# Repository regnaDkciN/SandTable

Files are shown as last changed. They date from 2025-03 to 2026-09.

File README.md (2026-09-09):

# **NOTE:** 
This GIT archive contains several versions of the sand table described within this document.  Each version contains different hardware and firmware capabilities.  The versions are:
* **MySandTable** - This was the original version and is described fully in this readme file.  It used the original Arduino board.
* **MySandTable2350** - This version upgraded to use the Adafruit Metro 2350 board.  This version contains many upgrades from the original.
* **MySandTableFreeRTOS** - This version uses the Adafruit Metro 2350 and adds FreeRTOS support.
* **MySandTableFreeRTOSExp** - This was originally an experimental version, hence the name, but has become the  main development version.  It has many upgrades and fixes many bugs.
* **MySandTableSdFat** -This version adds access to the Metro 2350 board's SD card.  It allows for placing new shape files in the SD and randomly selects files to shape execute.

# Sand Table
Sand Table
I have always been interested in sand tables, but most required more carpentry work than I could handle, and were too expensive for my budget.  Then I came across  the Instructable of [<u>World's First Cycloid Art Table: How I Built This Arduino-Powered Spirograph Machine</u> by NewsonsElectronics](https://www.instructables.com/Worlds-First-Cycloid-Art-Table-How-I-Built-This-Ar/).  This was finally a reasonable design that I could handle.

My background is in real time embedded firmware, so the software wasn't a problem.  Woodworking is pretty much out of my league.  However, this project was mainly laser cut, and my local library had a laser cutter available, so I learned how to use it with pretty good results.  Along the way I made quite a few changes to the design, and am pretty happy with the outcome.

This site describes some of the modifications I made on the way. Notable changes include:
* Addition of a home limit sensor with corresponding firmware.
* Addition of a 3D printed Arduino bumper for mounting the Arduino UNO board to the base.
* Addition of a top ring to hold a plexiglass window.
* Greatly modified Arduino sketch which adds many new shapes, randomization functions, and fixes several problems that were encountered with the original sketch.
* Addition of a power switch with associated 3D printable box.
* Replacement of the small wooden gears with new 3D printed ones.
* The highly modified original software version for use with the Arduino UNO - *MySandTable*.
* A software version - *MySandTable2350* - that replaces the Arduino UNO with an Adafruit Metro RP2350 board.  As of 21-AUG-2025 this branch will no longer be updated.
* A software version - *MySandTableFreeRTOS* - that uses the FreeRTOS real-time operating system on the Metro RP2350 board.  As of 21-AUG-2025 this branch will no longer be updated.
* A software version - *MySandTableFreeRTOSExp* - that plans motion several moves ahead in order to help smooth out the motion.  This version was originally experimental, thus the 'Exp' suffix.  However, it is currently stable and is the preferred RP2350 version.  All future development and fixes will be done on this version.
---
# General Issues/Fixes/Useful Information

This was my first experience with laser cutters.  The Instructable included .DXF and .SKP files for the laser cut parts.  I couldn't make use of the .SKP file, but found that I could work with the .DXF files.  For these I used [QCAD](https://qcad.org/en/) which is a free, open source application for 2D CAD drafting.  The available laser cutter required .PDF files though.  I ended up using QCAD to edit the original .DXF file and produce a .SVG file.  Then I used [Inkskape](https://inkscape.org/?about-screen=1) to convert the .SVG file to .PDF.  The workflow was as follows:
1. Use QCAD to edit the original .DXF file.
2. Use QCAD to generate the .SVG file.
2. Use Inkscape to add text and other features to the .SVG file.
3. Use Inkscape to change cut lines to 0.1pt width (required by the laser cutter).
4. Use Inkscape to create the .PDF file which is used by the laser cutter.

## Wood Selection
Used Baltic Birch Plywood- B/BB Grade 1/8" / 3mm / 24"x24"  (https://makerstock.com/).  Liked the quality of the wood and the price was reasonable.

## Steel Ball
Instructable showed both 15mm ball and 8mm ball.  I experimented and ended up replacing the steel ball with stack of 4 each [3mm x 2mm magnets](https://www.amazon.com/dp/B09SLFSRBP).

## Sand
I originally used the recommended sand in the table but found it to cause jerky ball motion, and was pretty noisy. After an extensive web search, found  that [Shuffleboard Sand](https://www.amazon.com/dp/B08NFZFGQF) was an excellent replacement.  This produces much smoother and quieter movement.

## Magnets
The Instructable used a single 15mm x 3mm magnet on the end of the linear arm.  I stacked 2 each 15mm x 3mm magnets for better ball following: (https://www.amazon.com/dp/B0B5G6XS4J).  At one point I tried 3 stacked magnets, but found that 2 worked just as well.

## Miscellaneous Table Construction
* I found that the motors didn't originally line up vertically.  This may have been due to my motors not being sized exactly as the specified ones, or due to my lack of construction skills.  At any rate, I ended up with 3 spacers under the center (linear) motor, and none above it.  I also used 1 spacer below the outer (rotary) motor and 2 spacers above it.  Due to this, the small pillar needed to be modified slightly to fit correctly in my setup.  I cut 3mm from lip that goes over servo to account for extra spacer below.
Modified Small Pillar
* The Instructable wasn't very clear about the number of small rings needed to hold up the table.  I used 8 layers of small rings, which also accounts for the extra magnet that I used.  Similarly, it wasn't clear how many large rings should be used on the table.  I settled on 5 large rings because I wasn't sure about the ball size.  However, after deciding on using 4 each of 3mm x 2mm magnets in place of a steel ball, it is clear that I could have used 4 rings instead.
Rings Callout
* After assembly, I found that the table wasn't securely attached to the base, so it was too easy to attempt to pick the unit up and have the table detach from the base.  I did not want the table to permanently connect to the base since I knew that maintenance would then be impossible.  I decided on the simple approach of drilling  1/16" holes in the table vertical rods, and insert a wire through the hole to keep the table attached to the base.  This allowed for easy  detachment of the table from the base by simply removing the wires from the rods.
Retaining Wire
* The original holes for the potentiometers were too close to the Arduino UNO board.  I moved them to the center of the corresponding boards.  I also added labels as shown below.  After some use, I decided that the pot labels would be better placed above the potentioneters, but left them as is.
 Front Low Level View
* I found that the potentiometer face plates were not very secure.  To fix this, I carefully drilled 5/64" holes through the faceplates and base plate and inserted small nails.
* I originally added rubber feet to the bottom of the base.  It turned out that they prevented easy shaking of the table to clear it, which is very useful when debugging.  I replaced the rubber feet with felt pads and found that these were much better.  The feet I ended up using were [these](https://www.amazon.com/Black-Self-Adhesive-Felt-Bumpers/dp/B07DYQJRDB/ref=sr_1_1?sr=8-1).
* I have added a 3D printed part - "Bezel3.stl" - to strengthen the face plate panels (the ones that hold the pots and the UNO face plate).  It contains a channel that the top of the face plate panels seat into and provides some rigidity.  It also helps to protect the wiring of the electronic parts.
Bezel

----

# GEARED PARTS
I had several problems with the gears.  This section contains information regarding my findings and fixes.

## Dowel Rods
I couldn't find the tapered dowel rods that were recommended in the Instructable write-up.  I ended up using [1/8" wooden dowel rods](https://www.amazon.com/dp/B0CXDDGRFK) for the geared parts .  This required changing all the dowel rod holes in the geared parts to 3 mm.  The "Modified Parts" files contain the modified parts.  Note that two of the large gear are required.

## Bearing
I couldn't find recommended bearing.  Instead I used a [F695-2RS Bearings, 5x13x4mm Ball Bearing](https://www.amazon.com/dp/B0CZ6RBJSZ) which worked out well.

## Reversed Linear Gear
I accidentally mounted the linear gear in the opposite direction from how the Instructable  video shows it.  This required several modifications to the Arduino sketch.  If you use my program, you may want to flip the linear gear as I did to avoid problems with my code.
Flipped Linear Gear

## Large Rotary Gear
* The Instructable was ambiguous regarding the large rotary gear.  I found that it should be doubled up (i.e. one on top of the other) and in my case I needed the center hole diameter to be 12.7mm.  The included  "Modified Parts" files have have been updated with these changes.  Note that two of the large gear are required.
* Neither of the laser cut small gears worked well.  Both were a little too wide, probably due to a difference in kerf width between the laser cutter I used and the one used in the Instructable.  I experimented and came up with 3D printed gears to replace both of them.
* Doubled Up Large Gear

## Small Gears
* The small outside (rotary axis) gear needed to be at least 5mm thick, which is OK since the large rotary gear is doubled up.  The included **Small Gear Thicker.stl** file can be used to 3D print  this thicker gear.  I used PLA for the gear with 30% infill and 0.2mm layer.  The PLA gear has worked great with over 100 hours of run time, but I would guess that ABS or PETG would be better.
* The small center (linear) gear did not catch the motor shaft enough and gave constant problems.  I created a new 3D printed gear which adds a 2.4mm long 11mm diameter shaft which fits in the center hole of the large gear, and gives more area of contact between the small gear and the motor shaft.  The included **Small Gear With Bushing.stl** file contains the result. I used PLA for the gear with 30% infill and 0.2mm layer.  The PLA gear has worked great with over 100 hours of run time, but I would guess that ABS or PETG would be better.

# Motors
* As previously mentioned, I had problems with motor height alignment.  I ended up with 3 spacers under the
  center motor, and none above.  Used 1 spacer below the outer motor, and 2 above.
  Rotary Motor Spacers
  Linear Motor Spacers
 
* I used these [Nema 17 stepper motors (17HS4023)](https://www.amazon.com/dp/B0C36D34F5).  Their original cables were too long which made it hard to stow them on the base.  I replaced the original motor cables with shorter [(500mm) stepper cables](https://www.amazon.com/dp/B07Q12B6K5?ref_=ppx_hzod_title_dt_b_fed_asin_title_0_0).  These solved the size problem, but weren't wired the same as the original cables.  In order to make them work, the 2 middle conductors needed to be swapped.  I just used brute force and pulled them out of on end, swapped them, then pushed them back in.  This worked OK and I have had no problems with them.

* The screws from the original motors were too short.  I replaced the center motor screws with m3 x 6mm, and the outer motor screws with m3 x 14mm.

* The holes in the motor spacers were too small.  I enlarged them using a 7/64" bit, which worked out well.

# CNC Shield
* I used the recommended [Arduino CNC Shield](https://www.amazon.com/dp/B08KFYKKN4).  In bringing it up I had several major issues.  Some were my fault, and some were due to the broken motor drivers that were included with the shield.  In the end, these were the problems and workarounds:
	+ Not one of the 4 included stepper drivers functioned at all.  In fact, one of the drivers caused the CNC shield's fuse to blow, and blew a trace to the X-Axis.  The Instructable recommended the use of other drivers, and I bought them, but I wanted to get it to work with the original drivers before I switched to the good ones.  I should have just started with the [TMC2209 Stepper Drivers]( https://www.amazon.com/dp/B08SMDY3SQ), and would recommend everyone do the same.  I ended up bypassing the fuse, and using the shield's Y- and Z-Axis instead of the X- and Y-Axis.  The Y-Axis now controls the linear in/out axis, and the Z-Axis now controls the rotary axis.
	+ The Instructables author also contributed two enhancements for the CNC shield which I applied to my setup. Neither of these enhancements is absolutely necessary, but I think they are useful.  Both of the modifications can be found at the Instructables site as [Arduino CNC Shield V3 - Enhanced Capabilities and Features](https://www.instructables.com/Arduino-CNC-Shield-V3-Enhanced-Capabilities-and-Fe/).  I modified the shield to supply power to the Arduino, and to add the ability to enable the axes individually (based on Y- and Z-Axes).

# Stepper Drivers
* The DRV8825 stepper drivers that came with the CNC shield were total junk.  Not a single one of them worked.  Trying to use one of them resulted in blowing the CNC shield fuse, and damaging the X-Axis socket.
* As recommended, I used [TMC2209 Stepper Drivers]( https://www.amazon.com/dp/B08SMDY3SQ) instead of the ones that came with the CNC shield.
* Setting the motor current of the TMC2209 stepper driver is well explained [HERE](https://www.youtube.com/watch?v=VcyGzXIZm58).  The desired current for these motors is less than 700mA per phase.

  		Vref = Desired Current x 0.71 x 2 
  		     = 0.99V for 700mA per phase
  		
# Arduino UNO
* I used the Arduino UNO that came with the CNC shield.
* Found that mounting the Arduino is difficult, especially when gear assembly is already in place.  Created a 3D printed Arduino bumper with side mounting holes to help in placing the Arduino.  See the included **Arduino Bumper.stl** file.
* Found that M3 screws fit nicely into 7/64" holes in plywood.  Used M3 screws to mount the Arduino with bumper to base plywood.
Arduino Mount

# Power Box
* I used this [Power supply: 12V 8A](https://www.amazon.com/dp/B0CL1RX1TX).  It is definitely overkill, but works well and was not too expensive.
* I wanted a clean way to connect power to the sand table, so I decided to use a 3D printed power box with a power connector that matched the power supply, and a switch.  The switch box with lid is included as **Power Box.stl** and **Power Box Lid.stl**.  Used PLA, 20% infill, and 0.2mm layer height for the print.
Power Box 1
Power Box 2
* I used this [Power supply connector](https://www.amazon.com/dp/B0D9JGXBJB).
* I used a switch that I had on hand, similar to [this one](https://www.amazon.com/uxcell-Position-Button-Rocker-Switch/dp/B0727PBJLV).
* Drilled two 3/16" holes through the base of the power box and the base of the sand table for mounting.  Used m3 x 5mm screws to secure the power box to the base.

# Rotary Home Sensor
* I wanted to be able to home the axes to a known starting position so that things like text could be displayed in a consistent manner.  So I added a home limit reed switch using GPIO 5.  This GPIO pin was originally the X axis direction pin, but since I am using Y and Z, the X axis direction pin was available.  Here's an example of some text that will always print upright due to the axes being homed.
JMC
* I used [Reed Switch Reed Contact Normally Open (N/O) Magnetic Induction Switch (2mm*14mm)](https://www.amazon.com/dp/B07RS2M9TR) to sense the pointer magnet.  There was no need to add any additional magnets.
* I created and 3D printed a mount for the reed switch, which is included as **Reed Switch Mount.stl** and mounted it near the Brightness pot. Used PLA, 15% infill, and 0.2mm layer height for the print.  Used m3 x 4mm screws to secure the mount to the horizontal member.   Drilled a 3/16" hole in the horizontal member near the mount to pass the sensor wires through to the Arduino.  Used 
Home Sensor Mount
* Updated the Arduino sketch Home() function to use new home limit switch.  See the .ino file.
* The Home() operation behaves as follows:
    ```
 	   Extend the in/out axis all the way out
	   If already on the home sensor
	       Then rotate CCW till off of the sensor
	   Rotate CW till the home sensor is detected
	   Rotate CCW by the amount specified by HOME_ROT_OFFSET
	   Retract the in/out axis all the way in
	   Initialize all position and motor variables to position (0,0)
	   Enable both motors
* Note that an offset may be applied (HOME_ROT_OFFSET) in order to align the rotation of the origin as desired.

# Miscellaneous Electronics
## Potentiometers
* I used these [10K pots](https://www.amazon.com/dp/B0BRGX2FTL).

## LEDs
* I use these [LEDs](https://www.amazon.com/gp/product/B0C8HTH282)
* Drilled a 5/32" horizontal hole into the upper ring to route LED cable into the ring vertical hole.
* Drilled a 5/16" hole in vertical support to pass LED cable through.
* Added a  [2 Conductor JST Connector](https://www.davesrce.com/product-page/jst-connectors?gQT=1) to attach the LEDs to the Arduino UNO so that top may easily be disconnected from base.
* Added a [Self-Adhesive Super Klip](https://www.amazon.com/Super-Glue-KW10-12-Klips-120-Pack/dp/B00FY8WHEU) as a cable organizer for the LED cable.
![LED Connector 1](https://i.imgur.com/DXwuwZe.jpeg)
![LED Connector 2](https://i.imgur.com/6Vc9H8k.jpeg)

## MOSFET 
* Used [Power MOSFET IRFZ44N](https://www.amazon.com/dp/B0CHQ8QJ5K).  Note that the parts list on the Instructable is incorrect and specifies BD139N transistor when IRFZ40N should be used.  IRFZ44N is an acceptable replacement.
* Added a 100K resistor between the MOSFET gate and ground (source) to keep the LEDs from turning on full brightness at power-up.
* Used metal 3mm x 8mm bolt to secure MOSFET to left Arduino mounting wing through hole drilled in base.  Also use 2  m3 washers for spacing and heat dissipation.
![MOSFET Mount](https://i.imgur.com/AMYUQlH.jpeg)

# Window
* Created a top outer ring that is used to hold the acrylic window.  The attached **Window Holder no Text.pdf** file corresponds to this window holder.
* Used [12" x 12" Clear Cast Acrylic Sheet]( https://www.amazon.com/dp/B0BBQ8B41F) for the window.  Cut it circular with laser the cutter using the attached **Window.pdf** file.  It fits inside top Window Holder ring.
* Found that the acrylic widnow generates enough static to attract the Shuffle Board Sand.  I don't know if real sand would have the same problem, but the shuffle board sand really did.  I was a little skeptical, but decided to try an [Anti-static CRT Cleaner](https://www.amazon.com/dp/B00UM9C04S?ref_=pe_123509780_1038749300_fed_asin_title) and found that it worked well and completely eliminated the problem with sand clinging to the acrylic window.  I would recommend its use.
* Generated simple 3D printed cylinders (**Window Knob.stl**) to use as knobs for the window.  Used PLA, 20%infill, and 0.2mm layer height for the print.  Attached them to the window with glue.
![Window Knob](https://i.imgur.com/bxLPUnK.jpeg)

# Software

The included Arduino sketch (**MySandTable.ino**) was based on the [Instructable]( https://www.instructables.com/Worlds-First-Cycloid-Art-Table-How-I-Built-This-Ar/) Arduino sketch **working10iteration.ino**.  It was, however, almost completely rewritten to add features and make it more understandable.  A few of the changes were:
* Re-formatted, including renaming variables and functions, using consistent indenting, and generally cleaning up the code.
* Uses Y- and Z-Zxes of the CNC shield instead of X- and Y- of the original.  This was due to the X-axis hardware on my CNC shield being damaged.
* Used some slightly different algorithms in a several spots.
* Added several more shapes, and randomization functions for each shape.
* Many more changes to fix anomalous behavior and enhance operation.

## Serial Logging
The **SerialLog.h** file was added to help with making groups of data logging to be easily enabled or disabled.  It contains macros to selectively print information based on some user-defined level macros.
Prints will only generate output if the corresponding macro is set to `true`.  `SerialLog.h` should be placed in the same directory as the Arduino sketch (`MySandTable.ino`).

Logging macros include:
* `LOGF(pBuf, bufSize, level, ...)` <br>
	This macro implements a formatted print.  It uses a printf style format to create a string to print.  The limitation of this macro is that it cannot print 32-bit integers or floats.  Its arguments are:<br>
&nbsp;&nbsp;&nbsp;&nbsp;`pBuf` : A pointer to a buffer to hold the formatted output data.<br>
&nbsp;&nbsp;&nbsp;&nbsp;`bufSize`: The size, in bytes, of `pBuf`.<br>
&nbsp;&nbsp;&nbsp;&nbsp;`level` : A value that will be evaluated as either `true` or `false`. If `true`, then the printf style string will be sent out the serial port.  
&nbsp;&nbsp;&nbsp;&nbsp;&nbsp;&nbsp;&nbsp;&nbsp;&nbsp;&nbsp;&nbsp;&nbsp;&nbsp;&nbsp;&nbsp;&nbsp;Otherwise no action will be taken.<br>
&nbsp;&nbsp;&nbsp;&nbsp;`args`: This is a printf style string with optional additional arguments.
* `LOGU(level, v)`<br>
	This macro implements an unformatted print.  It simply prints the given single value as long as `level` evaluates to `true`.  Its arguments are:<br>
 &nbsp;&nbsp;&nbsp;&nbsp;`level` : A value that will be evaluated as either `true` or `false`.  If `true`, then the value will be sent out the serial port.
&nbsp;&nbsp;&nbsp;&nbsp;&nbsp;&nbsp;&nbsp;&nbsp;&nbsp;&nbsp;&nbsp;&nbsp;&nbsp;&nbsp;&nbsp;&nbsp;Otherwise no action will be taken.<br>
&nbsp;&nbsp;&nbsp;&nbsp;`v`: This is the value that will printed if `level` evaluates to `true`.  It can be any valid printable data type.

The top of MySandTable.ino contains macros to enable/disable specific types of information to be sent via the serial port as well as macros to simplify logging macros use.
```
/////////////////////////////////////////////////////////////////////////////////
// S E R I A L   L O G   S E T T I N G S
//
// The following #defines are used in conjunction with SerialLog.h to selectively
// enable/disable printing of certain information.  Setting any macro to 'true'
// enables the specific level of data to be printed.  Setting any macro to 'false'
// disables printing of the specific data level.
/////////////////////////////////////////////////////////////////////////////////
#define LOG_DEBUG        false      // Log debug related info. Not normally  needed.
#define LOG_VERBOSE      false      // Log verbose info. Not normally needed.
#define LOG_INFO         true       // Log some useful extra info.
#define LOG_STEP         false      // Log data to help stepping ShapeArrays
#define LOG_CYCLES       true       // Log useful info regarding remaining cycles.
#define LOG_ALWAYS       true       // Log data unconditionally.
#define LOG_BUF_SIZE     60         // Important: size of formatted log buffer.
                                    // All formatted log strings are limited to
                                    // this size.
char LogBuf[LOG_BUF_SIZE];          // Buffer for formatting log data.

// Logging macros to ease log use.
#define LOG_F(level, ...)   LOGF(LogBuf, LOG_BUF_SIZE, level, __VA_ARGS__)
#define LOG_U(level, v)     LOGU(level, v)

```

* `LOG_DEBUG` - Setting this macro `true` will enable debug related information to be sent via the serial port.  This was mainly used to debug the SuperStar shape, and is normally set to `false` to disable sending its data.
* `LOG_VERBOSE` - Setting this macro `true` will enable verbose information to be sent via the serial port.  This was mainly used in early debugging of the movement generation code, and is normally set to `false` to disable sending its data.
* `LOG_INFO` - Setting this macro to `true` will enable informational data to be sent via the serial port.  The data sent by enabling this macro describes the call to the shape that is currently executing.  It includes the name of the function being executed, and a list of all of its arguments.  This macro is normally set to `true`. (A possible future project will use a Raspberry Pi Zero W to read this information, and save it along with a picture of the resulting table state.  Stay tuned.)
* `LOG_STEP`- Setting this macro `true` will enable the ability to single step the plotting of shape array data.  This can be useful for optimizing the memory footprint of any newly added shape array.  For example, by single stepping through a shape array, one may identify redundant or useless moves that may be removed.  This macro is normally set to `false`.
* `LOG_CYCLES`- Setting this macro `true` will generate cycle countdown information.  Certain shapes loop through multiple cycles before they complete.  Enabling this macro displays a countdown of the number of cycles remaining for the particular shape.  This macro is normally set to `false`, but if you like to have an idea of how much time is left when generating a shape, then set it to `true`.
* `LOG_ALWAYS` - This macro should always be set to `true`.  All data that should be sent unconditionally uses this macro.

A buffer that is used for formatting log data is also created here.  The buffer, `LogBuf[LOG_BUF_SIZE]`, must be sized large enough to handle the largest formatted log message.  `LOG_BUF_SIZE` is initially set to 60, which should be enough to handle all existing formatted log messages.

Two more macros (`LOG_F` and `LOG_U`) are also created here to make using the serial logger easier.  All logging done in MySandTable.ino uses one of these two macros.
 
 ## User Settable Constants
 The following macros are meant to be settable by the user depending needs.
 ```
 #define PAUSE_ON_DONE  false // Set to 'true' to pause when drawing finishes.
#define ROT_CAUSING_IN CCW   // Set to 'CW' if clockwise rotation causes IN movement.
                              // Set to 'CCW' if counter clockwise rotation causes IN movement.
```
 
* `PAUSE_ON_DONE` - This macro is used while debugging/testing.  If `true`, then execution will stop after each shape is drawn.  Execution will begin only after the Speed pot is turned fully CCW (the pause position), then  moved off of the pause position.<br>
* `ROT_CAUSING_IN` - Due to the mechanical configuration of the sand table, movement of the rotary axis causes a proportional move of the linear axis based on the direction of rotary rotation.  The firmware compensates for this movement.  In order for the compensation to function properly, the firmware must know which direction the linear axis moves in relation to the rotary axis.  (Due to an oversight on my part, my linear gear behaves opposite of the one in the original Instructable, thus needing attention).  This macro lets the firmware know which direction of rotary axis movement will cause the linear axis to move inward (toward zero).  Values for this macro should be either `CW` for clockwise, or `CCW` for counter-clockwise.  I believe the original Instructable hardware would use `CW`.  Since mine is reversed, I use `CCW`.
* `USE_HOME_SENSOR` - This macro can be used to disable the use of the home sensor in systems that don't use it.  Set to `true` if you are using a rotary home sensor.  Set to `false` otherwise.
 
The meaning of most of the rest of the constants should be obvious with the following
exceptions:
* `STEPS_PER_UNIT` - This macro specifies the number of interpolation steps used per unit distance.  For example, if `MAX_SCALE` equals 100 (the normal setting), then setting `STEPS_PER_UNIT` to 1 will cause each
interpolation step to be 1 unit in length.  Setting `STEPS_PER_UNIT` to 2 will cause each interpolation step to be 1/2 unit in length, and so on.<br>
* `HOME_ROT_OFFSET` - I added a rotary axis home sensor and firmware to use it.  The `Home()` function will rotate CW until it detects the home sensor.  Once at the home sensor position the rotary axis will rotate `CCW` for the number of servo motor steps specified by `HOME_ROT_OFFSET`.  This allows for a consistent startup position which can be handy when plotting coordinate array data like `JMCPlot[]`.<br>
* `WIPE_RATIO` and `WIPE_RASTER_INC` - These macros pertain to board clearing (wiping) operations.  The Instructable recommended both 15mm and 8mm ball.  After experimentation, I decided to use a stack of 3mm x 2mm magnets.  Each of these selections has a different footprint when plotting shapes.  Bigger balls create a wider path than smaller balls or disk magnets.  Depending on the marker used, a different width between successive wipe lines can be used.  (There is no need to keep lines very close when using a large ball).  `WIPE_RATIO` is used in `ClearFromIn()` and `ClearFromOut()` to affect a wipe that looks good, but takes the minimum amount of time to execute.  It specifies the ratio value that is passed to `MotorRatios()` to perform the wipe. `WIPE_RASTER_INC` is used by `ClearLeftRight()` for a similar purpose.  It specifies the number of units between successive wipe raster lines.  You may need to experiment with these values to find the best one for your setup.
* `FLOAT_PRECISION` - This specifies the precision that floats generated by `RandomFloat()` will use.  It is specified as 10 to the power of the number of significant digits desired.  For example, setting it to 100.0 will cause 2 significant digits, 1000.0 will cause 3 significant digits, and so on.  A good value seems to be 100.0.

A section of shape related constants specifies limits for many of the shape patterns.  They may be modified as desired.  Their meanings should be obvious.
```
// Shape algorithm limits.
const uint16_t MAX_CYCLES      = 50;        // Maximum cycles to generate when drawing.
const uint16_t MAX_STAR_POINTS = 40;        // Max number of Star() points.
const uint16_t MIN_STAR_POINTS = 3;         // Min number of Star() points.
const float    MAX_STAR_RATIO  = 0.95;      // Max ratio of Star() inside to outside points.
const float    MIN_STAR_RATIO  = 0.1;       // Min ratio of Star() inside to outside points.

const uint16_t MAX_POLY_SIDES  = 8;         // Max number of polygon sides.
const uint16_t MIN_POLY_SIDES  = 3;         // Min number of polygon sides.
const uint16_t MIN_POLY_SIZE   = MAX_SCALE_I / 4;
                                            // Min size of a polygon or star.

const float    MAX_MOTOR_RATIO = WIPE_RATIO;// Max motor ratio value.
const float    MIN_MOTOR_RATIO = 1.0 / MAX_MOTOR_RATIO;
                                            // Min motor ratio value.

const uint16_t MIN_CIRCLE_SIZE = MAX_SCALE_I / 4;
                                            // Min circle size.
const uint16_t MAX_CIRCLE_SIZE = MAX_SCALE_I;
                                            // Max non-lobed circle size.
const uint16_t MIN_CIRCLE_LOBES= 1;         // Min circle lobes.
const uint16_t MAX_CIRCLE_LOBES= 10;        // Max circle lobes.

const uint16_t MIN_SPIRO_FIXEDR= MAX_SCALE_I / 3;
                                            // Minimum spirograph fixed R size.
const uint16_t MIN_SPIRO_SMALLR= 8;         // Minimum spirograph moving circle radius.
const uint32_t SPIRO_NUM_POINTS= 300;       // Number of points to step for
                                            // spirograph shapes.
const float    SPIRO_ANGLE_BASE= PI_X_2 / (float)SPIRO_NUM_POINTS;
                                            // Base angle for spirograph shapes.

const uint16_t MIN_ROSE_VAL    = 1;         // Minimum rose shape num and denom values.
const uint16_t MAX_ROSE_VAL    = 20;        // Maximum rose shape num and denom values.
const uint16_t MIN_ROSE_SIZE   = MAX_SCALE_I / 4;
                                            // Minimum rose x/y size.
const uint16_t MIN_ROSE_RES    = 2;         // Minimum smoothness resolution.
const uint16_t MAX_ROSE_RES    = 64;        // Maximum smoothness resolution.

const uint16_t MIN_CLOVER_VAL  = 1;         // Minimum clover shape radius values.
const uint16_t MAX_CLOVER_VAL  = 10;        // Maximum clover shape radius values.
const uint16_t MIN_CLOVER_SIZE = MAX_SCALE_I / 4;
                                            // Minimum clover x/y size.
const uint16_t MIN_CLOVER_RES  = 6;         // Minimum clover resolution values.
const uint16_t MAX_CLOVER_RES  = 180;       // Minimum clover resolution values.

const uint16_t MIN_ELLIPSE_SIZE = MAX_SCALE_I / 4;
                                            // Minimum ellipse x-axis size;
const float    MIN_ELLIPSE_RATIO = 1.3;     // Minimum ellipse ratio.
const float    MAX_ELLIPSE_RATIO = 8.0;     // Mzximum ellipse ratio.

const uint16_t MIN_SERIES_STEPS = 1;        // Minimum number of series steps.
const uint16_t MAX_SERIES_STEPS = 12;       // Maximum number of series steps.
const uint16_t MIN_SERIES_INC   = 8;        // Maximum size increment for series.
const float    MAX_SERIES_ANGLE = 20.0;     // Maximum angle increment for series.

const uint16_t MIN_HEART_SIZE   = MAX_SCALE_I / 4; // Minimum heart size.
const uint16_t MIN_HEART_RES    = 8;        // Minimum heart size.
const uint16_t MAX_HEART_RES    = 128;      // Minimum heart size.
```

## Adding New Shapes
New shapes are generally implemented as 2 or 3 functions:
* The shape function is used to generate a shape given a specific set of arguments.  A good example is the `Polygon()` function:
```
/////////////////////////////////////////////////////////////////////////////////
// Polygon()
//
// Create a polygon of a specific size.
//
// Arguments:
//   - numSides : Number of sides the polygon will have.
//   - size     : Size of the polygon.
//   - rotation : How much to rotate the polygon, in radians.
/////////////////////////////////////////////////////////////////////////////////
void Polygon(uint16_t numSides, uint16_t size, float rotation)
{
    // Make sure all arguments are within valid limits.
    numSides = constrain(numSides, MIN_POLY_SIDES, MAX_POLY_SIDES);
    float scale = (float)constrain(size, MIN_POLY_SIZE, MAX_SCALE_I);

    // Loop to create the (possibly rotated) polygon.
    for (uint16_t i = 0; i <= numSides; i++)
    {
        float angle = rotation + (PI_X_2 * (float)i) / (float)numSides;
        GotoXY(scale * cosf(angle), scale * sinf(angle));
    }
} // End Polygon().
```
* An (optional) random function is used to generate some valid random arguments for the shape and call the shape with the generated random arguments.  Most shapes have associated random functions.  For example the `RandomPolygon()` function (which is no longer used):
```
/////////////////////////////////////////////////////////////////////////////////
// RandomPolygon()
//
// Calls Polygon() with some random values.
/////////////////////////////////////////////////////////////////////////////////
void RandomPolygon()
{
    // Generate some legal arguments for the call to Polygon().
    uint16_t sides = random(MIN_POLY_SIDES, MAX_POLY_SIDES + 1);
    uint16_t size   = random(MIN_POLY_SIZE, MAX_SCALE_I + 1);
    float    rot    = RandomFloat(0.0, PI_X_2);

    // Show our call.
    LOG_F(LOG_INFO, "Polygon(%d,%d,", sides, size);
    LOG_U(LOG_INFO, RtoD(rot));
    LOG_U(LOG_INFO, ")\n");

    // Make the call to Polygon().
    Polygon(sides, size, rot);
} // End RandomPolygon().
```

* An (optional) series function generates a series of the shape, starting with a random set of arguments, then  increasing the size and angle on successive calls.  The series is generally used with simple shapes that don't repeat for multiple cycles.  For example, `Heart()`, `Polygon()`, `Star()`...  Here is an example:
```
/////////////////////////////////////////////////////////////////////////////////
// PolygonSeries()
//
// Create a series of polygons vith varying size and rotation.
/////////////////////////////////////////////////////////////////////////////////
void PolygonSeries()
{
    LOG_U(LOG_INFO, "PolygonSeries()\n");

    // Generate some legal arguments for the calls to Polygon().
    uint16_t sides = random(MIN_POLY_SIDES, MAX_POLY_SIDES + 1);
    uint16_t size  = random(MIN_POLY_SIZE, (3 * MAX_SCALE_I / 4) + 1);
    float    rot   = RadAngle;

    // Determine how many steps to take, and how much to increase size and angle.
    uint16_t steps = 0;
    uint16_t sizeInc = 0;
    float    rotInc = 0.0;
    GenerateSeriesSteps(size, steps, sizeInc, rotInc);

    // Loop to create the polygon series.
    for (uint16_t i = 0; i < steps; i++)
    {
        LOG_F(LOG_INFO, "Polygon(%d,%d,", sides, size);
        LOG_U(LOG_INFO, RtoD(rot));
        LOG_U(LOG_INFO, ")\n");

        // Make the call to Polygon() and increment our size and rotation.
        Polygon(sides, size, rot);
        size += sizeInc;
        rot += rotInc;
    }
} // End PolygonSeries().
```

To add a new shape, do the following:
*  Create the shape function (`Shape()`).
* For simple shapes, like Star or Polygon, a series function is often a good choice.  For complex shapes, like Spirograph, a randomization function is a good choice.  For shapes that are different based on single or series use, like Circle, both functions may be needed.
* Optionally create a randomization function for the shape (`RandomShape()`).  Generally, a shape will use at least one randomization function or series function.  
* Optiionally create a series function for the shape (ShapeSeries()).
* Add an entry to the `RandomShapes[]` array for the randomization and/or series function.
```
/////////////////////////////////////////////////////////////////////////////////
// RandomShapes[]
//
// This is an array of ShapeInfo instances which is used to select random shapes
// to be displayed.
/////////////////////////////////////////////////////////////////////////////////
ShapeInfo RandomShapes[] =
{
    ShapeInfo(RandomRatios, 10),
    ShapeInfo(RandomSpirograph, 0),
    ShapeInfo(RandomSpirograph2, 0),
    ShapeInfo(RandomSpirographWithSquare, 10),
    ShapeInfo(RandomRose, 11),
    ShapeInfo(RandomClover, 11),
    ShapeInfo(RandomSuperStar, 25),
    ShapeInfo(RandomCircle, 15),
    ShapeInfo(RandomPlot, 20),
    ShapeInfo(PolygonSeries, 10),
    ShapeInfo(StarSeries, 10),
    ShapeInfo(HeartSeries, 15),
    ShapeInfo(EllipseSeries, 10),
    ShapeInfo(RandomWipe, 30),
    ShapeInfo(RandomLines, 50)
}; // End RandomShapes[].
```
* `RandomShapes[]` entries consist of a pointer to the associated function, and a delay value.  The delay value specifies the number of execution cycles that must elapse between executions of the shape.  That is, some shapes should not be generated very often.  This value keeps the shape from occurring too frequently.  For example, wipes should be done rarely, so the delay value used for `RandomWipe()` is 30.  This means that at least 30 other shapes must be displayed before another wipe occurs.

## Random Seed 
At the end of `setup()`, a seed for the random number generator is fed to `randomSeed()`.  A new function was added - `GenerateRandomSeed()` - that generates better random seed values using an unused analog input pin (A2).  This helps to insure that each power-up will generate unique patterns.  The random seed value is logged to the serial port so that it may be saved if needed.  A serial port interface has been added which  allows re-seeding the random number generator to any value.  This provides the ability to manually set the random number generator to a previously reported value in order to duplicate a particular run pattern.
```
    // Seed the random number generator.
    RandomSeed = GenerateRandomSeed();
    randomSeed(RandomSeed);
```

## First Run
The first execution of `loop()` is setup to wipe the board, then display my initials.  This should be taken as an example of what is possible to accomplish at startup.  Feel free to change or remove this code as needed.                
```
    // On first iteration after boot, we wipe the board and display my initials.
    static bool firstTime = true;
    if (firstTime)
    {
        // Wipe the board.
        ClearFromIn();

        // Change this as desired.  It is the power-up greeting.
        RotateToAngle(atan2f((float)JMCPlot[0].y, (float)JMCPlot[0].x));
        PlotShapeArray(JMCPlot, sizeof(JMCPlot) / sizeof(JMCPlot[0]), false);

        // Delay a while to let the user view your awesome work!
        delay(5000);
        firstTime = false;
    }
```

## Remote Command Interface
Limited capability to control the sand table remotely via the serial port was added.  The following commands are accepted (see HandleRemoteCommands() for implementation):
* 'F' (FASTER)      Increase the speed.
* 'S' (SLOWER)      Decreases the speed.
* 'Q'               Restores speed control to the local speed pot.
* 'B' (BRIGHTER)    Increases the LED brightness.
* 'D' (DARKER)      Decreases the LED brightness.
* 'L'               Restores LED control to the local LED pot.
* 'P' (PAUSE)       Pauses motion.
* 'U' (UNPAUSE)     Unpauses motion.
* 'R 'newSeed'
    (RANDOM SEED) Re-seeds the random number generator with the value of
                  'newSeed', homes the axes and clears the board.
* 'G' (GET)         Get the last random seed.
* 'N' (NEXT)        Aborts the current shape and starts the next one.
* 'K' (KEEP ALIVE)  Kicks the watchdog.  If no messages are received from the 
                  serial port after REMOTE_TIMEOUT_MS milliseconds, then all
                  remote settings get cleared and local control is restored.
 
# Conclusions
This has been a great project.  I am very happy with the results.  It gave me a chance to learn more about laser cutting and some useful tools for it.  I would recommend it to anyone with moderate electronics skills.  However, there are a few things I would consider doing differently if I were to make another sand table.
* The Arduino UNO is somewhat under powered for this project.  It is relatively slow by today's standards, and is very memory limited.  For example, MySandTable.ino uses 90% of the Arduino's memory, and runs a little choppy on some of the more complex shapes.  There are two ways to approach this problem.  First, one could offload shape generation code to another processor which could communicate with the Arduino via its USB port.  The Arduino would then only contain communication and motor driver code.  This is the path taken by [another sand table design I've seen](https://github.com/DIY-Machines/Kinetic-Sand-Art-Table).  This is not a bad approach, but it is more expensive, and requires maintaining 2 separate code bases.  I prefer a second path which would be to use a better processor.  The [Adafruit Metro 2350](https://www.adafruit.com/product/6003) is a (mostly) drop in replacement for the Arduino UNO board, but it uses the Raspberry Pi 2350 processor which is almost 10 x as fast and has many times more memory.  This is a great replacement for the UNO, but requires a few firmware changes.  I have completed this update, and will document it in a future project.
* I might consider making the table a bit bigger.  The size of this table is a bit small, and the motors can certainly handle larger parts.  The limit for me would be the size of work pieces that the laser cutter is capable of.
* I would consider painting the bottom of the table black in order to make the sand shapes stand out more.  (I'm not sure if this is a good idea or not, but I'd try it anyway).
* I would update the laser files to add holes that I manually drilled.
* I would relocate the power box to have easier access to the power switch.
* I would consider adding a few buttons to things like abort the current shape, pause, and reboot.  Of course the software would need to change to accommodate these buttons.
* I am considering starting a new project that would automatically take pictures of the table after each shape completes.  This project would use a [Raspberry Pi Zero 2W](https://www.raspberrypi.com/products/raspberry-pi-zero-2-w/)  or [ESP32 CAM](https://www.instructables.com/Getting-Started-With-ESP32CAM-Streaming-Video-Usi/) which would communicate with the Arduino via USB and would log the startup random seed, the shape being displayed and all of its arguments as well as a picture of the resulting board.  It would be capable of being accessed via a web page.  Stay tuned for more.

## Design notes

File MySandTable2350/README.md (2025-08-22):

Upgrading from Arduino UNO to Adafruit Metro RP2350 (A Case Study)
===
Headline

**As of 21-AUG-2025 this branch will no longer be updated, but is kept for historical design info.**

This document describes the code and hardware changes that were needed to migrate a non-trivial Arduino UNO application to the Adafruit Metro RP2350 board.  Most readers will be familiar with the Arduino UNO, so it will not be described here.  The Adafruit Metro RP2350 is very close to a drop-in replacement for the Arduino UNO, but with a few differences that need to be accounted for.

The Adafruit Metro RP2350 is a tremendous improvement in processor speed and memory size over the Arduino UNO.  Here is a comparison of some of the more important features of each board:

| |  Arduino UNO |  Adafruit Metro RP2350  |
| :--- | :--- | :--- |
| CPU | ATMega328P | Dual Cortex M33 or Dual RISC-V
| CPU Voltage | 5 V | 3.3 V |
| CPU Speed | 16 MHz | 150 MHz |
| Bus Width | 8 Bits | 32 Bits |
| Flash Memory | 32 KB | 16 MB |
| RAM | 2 KB | 528 KB |
| Floating Point Processor (FPU) | No | Yes|
| Programmable I/O (PIO) | 0 | 12 |
| GPIO | 20 | 23 | 
| Analog Inputs | 6 | 6 |
| Micro SD Card Slot | No | Yes |
| Onboard RGB Neo Pixel | No | Yes |
| USB Type | USB B | USB C |

## The Application
A recent Instructable presented the [World's First Cycloid Art Table: How I Built This Arduino-Powered Spirograph Machine by NewsonsElectronics](https://www.instructables.com/Worlds-First-Cycloid-Art-Table-How-I-Built-This-Ar/). 

Sand Table

 This sand table uses laser cut parts and is driven by an Arduino UNO.  I had been looking for an affordable sand table project and this one fit the bill.  During the construction of the sand table, I noted a few areas that needed clarification, and some areas for improvement.  These are documented [here](https://github.com/regnaDkciN/SandTable).  One of the major issues I noted was that the Arduino UNO is somewhat under powered for this application with it's relatively slow processor and very limited memory size.  For example, my updated Arduino program for the sand table used nearly 100% of both flash and RAM, leaving no room for the future addition of shapes or other firmware improvements.  In addition, the calculations to generate certain shapes caused some some jerky servo motion which was partially due to the slow Arduino UNO.

## Adafruit Metro RP2350 to the Rescue
The Adafruit Metro RP2350 has the same physical size and shape as the Arduino UNO, and has (almost)  the same pinout.  More on that later.  This allows the Metro to work with the Arduino CNC shield without changing almost anything.  The following sections describe the changes, some required and some not, that I made to the sand table firmware and hardware.  I am quite pleased with the results.

### Data Type Changes
Since the UNO was tight on space, all data types were originally declared as the smallest size that would do the job in the UNO program.  In most cases ```(u)int16_t``` was used since the UNO compiler uses 16-bit integers as its native int size.  Using the native integer size saves on both memory size and execution time since using a different sized integer requires the compiler to generate and execute extra code.

The RP2530 that is used by the Metro has lots of memory compared to the UNO and its native integer size is 32-bits.  Therefore, when using the RP2350,  memory size is unimportant, and execution speed becomes the major goal.  As a result, almost all integer data types were changed to fast types.  For example, ```uint16_t``` becomes ```uint_fast16_t```, etc.  The _fast_ data types allow the compiler to use an integer size that is as least as large as the specified size, but may be larger if larger integers are faster on the particular machine.  In the case of the RP2350, since the native integer size is 32-bits, a ```(u)int_fast16_t``` will actually use 32-bits, but the same compiled for the Arduino UNO will use 16-bits.

### Speed Delay Value Changes
The UNO program set the timer clock period to 4 microseconds (uSec).  The default RP2350 timer clock period is 1 uSec.  To account for this, all speed delay values were multiplied by 4.  For example ```SPEED_DELAY_MIN_VAL``` was changed from 25 on the UNO to 100 on the RP2350, etc.  Speed increments in  ```HandleRemoteCommands()```  were also adjusted by a factor of 4.

### Changed Servos from 8 Microsteps to 64 Microsteps
With the RP2350's speed and native 32 bit integers, it was possible to improve the servo microstepping from 8 to 64.  This provides smoother and quieter servo movement.  However, this also now requires that the fastest servo moves occur at a 25 microsecond rate.  This is far too fast for the Arduino UNO, but the RP2350 can handle it with no problems.

Both hardware and firmware changes were required for this improvement:
* Hardware wise, a jumper was added to the M1 pins under each of the TMC2209 driver boards.  This selects 64 step microstepping.  This may be a bit confusing since the Arduino CNC shield and the TMC2209 use different labeling for the microstepping pins.   The pin that the Arduino CNC shield labels M1 actually corresponds to the pin that the TMC2209 refers to as MS2.  In any case, the jumper needs to be placed on the middle microstep pin of the Arduino CNC shield .

	Microstep Jumper
* Firmware wise,three changes were needed:
	-  All step related variables and constants needed to change to 32 bit integers since the maximum step count now exceeds the limits of a 16 bit integer.
	-  All step related constants needed to be multiplied by 8 to account for the 8 times increase in microstepping.	
	-  All speed related delay constants needed to be further divided by 8 to account for the microstepping change.

```
const int_fast32_t  ROT_TOTAL_STEPS   = 8 * 16000;  // Rotation axis total steps.
const int_fast32_t  INOUT_TOTAL_STEPS = 8 * 4300;   // In/Out axis total steps.
const uint_fast32_t HOME_ROT_OFFSET   = 347 * (ROT_TOTAL_STEPS / 1000);
...
volatile int_fast32_t InOutSteps   = 0;      // Current # steps in/out is away from 0.
int_fast32_t          InOutStepsTo = 0;      // Number inout steps needed to reach target.
volatile int_fast32_t RotSteps     = 0;      // Current # steps rotary is away from 0.
int_fast32_t          RotStepsTo   = 0;      // Number rotary steps needed to reach target.
...
const int_fast16_t  SPEED_DELAY_MIN_VAL = 100 / 8;   // Minimum axis moving delay value (uSec).
const int_fast16_t  SPEED_DELAY_MAX_VAL = 2000 / 8;  // Maximum axis speed delay value (uSec).

```

### Different Timer Handling
The UNO needs the timer clock rate to be set up before use as follows:
```
        TCCR1A = 0;           // Init Timer1A (for rotation motor).
        TCCR1B = 0;           // Init Timer1B (for in/out motor).

        TCCR1B |= B00000011;  // Prescaler = 64. (4 microsecond tick).
        OCR1A = 1000;         // Timer Compare1A Register.
        OCR1B = 1000;         // Timer Compare1B Register.

        TIMSK1 |= B00000110;  // Only use one interupt.
```

The RP2350 already has its timer running at 1MHz, so doesn't require any further initialization.

### Different Interrupt Handling
The UNO used a simple interrupt setup with ```ISR(vector)``` indicating that an interrupt will be handled by the function.  For example, the following outline shows how the UNO Interrupt Service Routines ( ISRs) were defined:
```
        // Timer 1A interrupt handler.
        ISR(TIMER1_COMPA_vect)
        {
            OCR1A = TCNT1 + RotDelay;
            ...
            ISR code
            ...
        }
        
        // Timer 1B interrupt handler.
        ISR(TIMER1_COMPB_vect)
        {
            OCR1B = TCNT1 + InOutDelay;
            ...
            ISR code
            ...
        }
```

The RP2350 handles timer interrupts more normally in that the ISR must be declared before use, and added to the timer list before it can be used as follows:
```
        int64_t RotaryServoIsr(__unused alarm_id_t id, __unused void *user_data);
        int64_t InOutServoIsr(__unused alarm_id_t id, __unused void *user_data);
        
        .
        .
        .
        
        void setup()
        {
        	 . . .
        	add_alarm_in_us(1000000, RotaryServoIsr, NULL, false);
       	 	add_alarm_in_us(1000000, InOutServoIsr,  NULL, false);
        	. . .
        }
        
        // Rotary servo ISR.
        int64_t RotaryServoIsr(__unused alarm_id_t id, __unused void *user_data)
        {
            ...
            ISR code
            ...
            return -RotDelay;
        }
        
        // Linear servo ISR.
        int64_t InOutServoIsr(__unused alarm_id_t id, __unused void *user_data)
        {
            ...
            ISR code
            ...
            return -InOutDelay;
        }
```

In order for the interrupt to repeat periodically, the UNO bumps the corresponding ```OCR1x``` register value at the start of each ISR as shown above.  For the RP2350 ISR to repeat, it returns the delay value from its ISR as a negative value, as shown above, indicating that the next execution should start exactly that many microseconds after the time the current ISR was triggered.

### Random Seed Generation
The latest UNO implementation of the sand table used an open analog input and a function - ```GenerateRandomSeed()``` - to generate a random seed at startup.  The RP2350 has a hardware based true random number generator with a standard function - ```get_rand_32()``` - to generate a 32-bit  random number.  So ```GenerateRandomSeed()``` was removed for the RP2350 version.

  ### API Math Function Differences
The Arduino UNO API supplies a ```squaref()``` function to square a float value.  This function is replaced in the RP2350 API with a function named ```sq()``` that does the same thing. So uses of ```squaref()``` were changed to ```sq()```.

  ### Execution Speed Differences
The rotary servo ISR contains logic to generate compensation pulses in the in/out servo proportional to the rotary axis movement.  Part of this logic uses a short delay to affect a pulse on the in/out servo.  In the UNO, a pulse delay of 1 microsecond was used.  Due to the slow speed of the UNO processor, this delay plus the surrounding code was sufficient to generate a pulse long enough for the servo driver hardware to handle.  However, since the RP2350 is so much faster, it was feared that the generated pulse might be too short, so the pulse delay was changed to 5 microseconds.  This was probably not necessary, but was done just in case

**UPDATE:** The latest version of the sand table firmware uses the the PIO state machines of the RP2350 processor to generate servo step pulses.  New file - STStepper.pio and STStepper.pio.h - implement the servo stepping logic.  Each step now uses the state machine to do the following for each step:
1. Set the servo's direction.
2. Delay 1 uSec.
3. Toggle the step pin high.
4. Delay 6 uSec.
5. Toggle the step pin low.
6. Delay 6 uSec.

As a result of using the PIO state machines, the servo ISR's were modified to step on each call rather than on every other call.  This allows the ISR to be called half as often as before, which leaves more execution time for other things.

The Arduino IDE does not directly handle compiling the STStepper.pio file to the STStepper.pio.h file.  In order to generate the STStepper.pio.h file from the STStepper.pio file, the STStepper.pio file was added to a Visual Studio Code project, it was compiled, then the generated STStepper.pio.h file was copied to the MySandTable2350 directory.

  ### GPIO Differences
The Arduino UNO firmware uses D12 as the enable for the rotation axis.  However, the Metro RP2350 uses D12 for HSTX connectivity.  The pin that used to be occupied by D12 is now D22.  As a result, the RP2350 code was changed to initialize D22 as the rotation axis enable output instead of D12.

### Added Pause Indication
The Metro RP2350 board contains a red LED that comes in handy in the sand table application to indicate that the axes are pausing, i.e. when the speed knob is turned to its lowest level, or paused via a remote serial command.  This was a simple change and provides some welcome feedback to the user.
```
const int PAUSE_LED_PIN      = PIN_LED;     // Pause LED lights red when paused.
...
bool UpdateSpeeds()
{
     ...
      // Indicate if we're pausing.
    digitalWrite(PAUSE_LED_PIN, !keepRunning);
    ...
}
...
void setup()
{
    ...
    pinMode(PAUSE_LED_PIN, OUTPUT);
    ...
}
```

  ### Serial Logging
The SerialLog.h file provided the ability to selectively log data to the serial port based on the value of user selectable macros.  The major problem with the UNO implementation is that the API did not provide a ```printf()``` function, and the ```sprintf()``` function provided by the UNO API did not handle 64-bit integers or floating point numbers.  As a result, many places in the sand table code resorted to clumsy sequences of log generation.  For example, the following code appears in the UNO version of the ```PlotShapeArray()``` function:
```
            // Display the current index and position.
            LOG_F(LOG_STEP, "%d   ", i);
            LOG_U(LOG_STEP, x);
            LOG_U(LOG_STEP, ",");
            LOG_U(LOG_STEP, y);
            LOG_U(LOG_STEP, "\n");
```

This was necessitated due to the UNO ```sprintf()` function not supporting floats.  The RP2350 API provides a fully operational ```printf()``` function that can handle all data types.  As a result, the SerialLog.h file was replaced with SerialLog2350.h which handles the logs more gracefully.  For example, the above 5 log statements were replace with the following in the RP2350 code:
```
            // Display the current index and position.
            LOG_F(LOG_STEP, "%d   %.1f,%.1f\n", i, x, y);
```

### Temporarily Handle Compiler Floating Point Issue
**NOTE:  As of 02-AUG-2025 this issue has been fixed on all RP2350 versions of the sand table software.  This requires version 4.6.1 or later of the Raspberry Pi Pico/RP2040/RP2350 API by Earle F. Philhower, III.**

I initially spent about an hour trying to find out why certain shape paths were not being generated correctly in my first try of the RP2350 code.  I eventually discovered that some floating point trig operations were sometime returning incorrect values.  After a web search, I came across the [RP2350 FPU compiler issue #2429](https://github.com/raspberrypi/pico-sdk/pull/2429).  It looks like this issue has been fixed on a development branch, but has not been released to production code yet.  Until it is fixed, my workaround is to change all floats to doubles, and change all float function calls to their double equivalent.  This naturally makes the code execution slower, so I will undo these changes once a good version of the compiler is released.  Here are the changes that will be needed:

| Double Function | Float Function |
| --- | --- |
| ```double``` |  ```float_t``` |
| ```cos()``` |  ```cosf()``` |
| ```sin()``` | ```sinf()``` |
| ```hypot()``` | ```hypotf()``` |
| ```atan2()``` | ```atan2f()``` |
| ```round()``` | ```roundf()``` |
| ```trunc()```| ```truncf()``` |
| ```sqrt()``` | ```sqrtf()``` |
| ```pow()```  | ```powf()``` |
 
### 3.3 Volt vs 5 Volt Processor Differences
The Arduino UNO is a 5 volt device.  The RP350 runs at 3.3 volts.  The original design fed the speed and brightness pots from the UNO's 5V source.  While the Metro RP2350 has a 5V output pin, it should not be used with the analog inputs (or GPIO pins for that matter).  The simple change was to move the 5V pot connection to the CNC shield 3.3V pin (next to the RST pin).

### Make MOSFET Handle 3.3V
The MOSFET used for the UNO version (IRFZ44N) has a Gate Threshold Voltage (VGS) of 2 - 4 volts.  This is a little too high for the 3.3V used by the RP2350.  The MOSFET would not fully turn on with the 3.3V gate.  The IRFZ44N was replaced with the [IRLZ44N](https://www.amazon.com/dp/B0CBKH4XGL) which has a VGS of 1-2 volts.  This allowed the MOSFET to turn on fully.  Also added a 100K resistor between the gate and source to keep the MOSFET from conducting at power-up before ```setup()``` could run.

### Work Around Analog Input Noise
Significant noise was found on the RP2350 analog inputs.  This showed up as LED flicker at lower brightness levels.  To compensate for this, the pot readings (analog inputs) were configured with a resolution of 12 bits, then shifted right by 4 bits after reading.  This effectively produced an 8 bit resolution, which is fine for the sand table application, but eliminated most of the noise/flicker issue.
 
Also changed the PWM (LED) output frequency to 100,000 to help reduce flicker.

```
// Potentiometer related constants.
const int_fast32_t  PWM_FREQ            = 100000; // PWM frequency.
const int_fast16_t  ANALOG_RESOLUTION   = 12;     // Number of ADC bits.
const int_fast16_t  ANALOG_SHIFT_FACTOR = 4;      // Amount to shift analog pot readings
                                                  // to mitigate ADC jitter.

setup()
{
    ...
    // We set the PWM frequency to 100 khz and set the ADC resolution to 12 bits
    // (4096 counts) to help reduce LED flicker at low LED knob settings.
    analogWriteFreq(PWM_FREQ);
    analogReadResolution(ANALOG_RESOLUTION);
    ...
}

inline uint_fast16_t ReadAPot(int pot)
{
    return analogRead(pot) >> ANALOG_SHIFT_FACTOR;
} // End ReadAPot().
```
### Account for Physical Differences
The Metro RP2350 includes an SD card holder and a power switch among other hardware that the UNO doesn't have.  These are physically located at the edges of the card.  The 3D printed bumper used to mount the card to the sand table was modified in order to allow the use of the SD card and power switch if desired.  The "Metro_2350_Bumper" files reflect these changes.

Notches

The Arduino UNO uses a USB-B connector while the Metro RP2350 uses a USB-C connector.  This required the face plate USB hole to be slightly lowered and re-sized to accommodate a USB-C connector.  The face plate USB hole was lowered by 2 mm and its height reduced to 10 mm.  The "Faceplate 2350" files reflect the changes.

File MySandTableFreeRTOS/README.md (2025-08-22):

Upgrading RP2350 Based Sand Table to FreeRTOS
===
Sand Table

**As of 21-AUG-2025 this branch will no longer be updated, but is kept for historical design info.**

This document describes the firmware design and code changes that were made to the [RP2350 based Sand Table](https://github.com/regnaDkciN/SandTable/tree/main/MySandTable2350) to use the [FreeRTOS](https://www.freertos.org/) real time operating system (RTOS).

## Motivation
In my opinion, replacing the sand table's Arduino UNO with an [Adafruit Metro RP2350](https://www.adafruit.com/product/6003) is well worth the extra expense.  The UNO provides acceptable basic operation, but its severely limited memory size and processor speed leaves little room for expansion and upgrades.  Using the RP2350 eliminates these problems, but the *MySandTable2350* software version does not take advantage of the RP2350's two core design.  For example, the potentiometers and serial port are polled and serviced while waiting for moves to complete.  This leads to some motion glitching (i.e. not being as smooth as it could be).  

FreeRTOS offers many features that can improve the sand table performance and take better advantage of the RP2350 processor architecture.  For instance:
* Code may be easily assigned to prioritized tasks that can run concurrently and take advantage of what would otherwise be processor idle time.
* Code may easily be assigned to run on either of the RP2350 cores, thus sharing the execution burden between the two cores.
* Software timers (alarms) may be used to generate the interrupts that handle servo updates.
* Tasks may communicate with each other via queues (and other mechanisms).  This allows tasks to eliminate most busy/wait loops and free up CPU cycles.
* Tasks can easily synchronize with each other as needed via several types of semaphores and other mechanisms.

## System Redesign
Some major changes to the software design were needed In order to take advantage of the RP2350's two cores and FreeRTOS's multitasking capabilities.  To understand the changes, it is necessary to understand the original design.

### Original Design (Before)
The original software was implemented as a single execution loop complemented by two interrupt service routines (ISRs) that directly controlled the rotary and in/out servos.   ```MotorRatio()``` moves are strictly handled by the ISRs, so there is no problem with them.  However, all other moves suffer from possible motion glitching as shown in the timing diagram below:



The above timing diagram attempts to show a greatly simplified and exaggerated  timing diagram of the original sand table software.  Important points are:
* The bottom timeline is used for timing reference and has no absolute relation to actual system timing.
* The top line (ISRs) represents ISR execution.  The sand table software actually uses two ISRs, one for rotary, and one for in/out.  The diagram shows a single ISR.  This is sufficient to explain the motion glitch behavior. In the diagram, the ISRs run periodically every 20 timing units.  When there is no motion to execute, they return quickly.  When motion is in process execution takes longer.
* The loop() line shows a greatly simplified ```loop()``` function behavior.  For our purposes, we are only concerned with move generation and polling for motion completion.  It only executes when the ISRs are not running.
* The timing starts with motion ISRs idle and ```loop()``` generating the next move.
* At time 30, the first move calculation has completed and the ISRs are commanded to start the move.   At this time, ```loop()``` starts polling the pots to update the speed and brightness values, checks the serial port for incoming requests, and starts polling for motion completion.
* At time 40 the ISRs see the move request and begin executing the move. ```loop()``` continues updating speed and brightness values, checking serial requests, and checking for completion of the move.
* This repeats with the ISRs performing the move and the ```loop()``` code polling until at time 86 the ISRs signal that the move has completed.  At this point, ```loop()``` is in the middle of its polling, which does not complete until time 110 at which time it begins calculations for the next move.  By this time, the ISRs have executed and seen no motion request, so simply return without doing anything.
* The ```loop()``` function takes some time generating the position for the next move, and doesn't make the next move request until time 150.  By this time several more idle ISR times have elapsed, which further disturb the smoothness of the motion.
* The cycle repeats after this.

It can be seen from the above that there is room for improvement.

### New Design (After)
#### Motion
The redesign takes advantage of both of the RP2350 cores as well as FreeRTOS multitasking.  The code has been broken up into the following tasks:
* Shape Task - This task selects random shapes and generates and executes shape moves.  It executes on core 0 at a priority level of 5.  This priority was selected to be the highest on core 0 so that the ```loop()``` function that executes at priority 4 won't interfere with (preempt) it.
* Print Task - This task handles all outgoing serial port traffic.  All serial logging and status data is sent via this task.  It executes on core 1 at a priority of 2.  This task shares its priority with the Remote Command Handler Task.  Both execute infrequently, and neither has critical timing requirements.
* Remote Command Handler Task - This task waits for incoming serial data and handles any command requests.  It executes on core 1 at a priority of 2.
* Read Pots Task - This task continuously polls the potentiometers (pots) and updates the servo speed and LED brightness.  It executes on core 1 at a priority of 0.  The priority of this task is low.  It executes when nothing else on core 1 is running.  It shares its priority with the idle task so that the idle task can get a chance to run periodically.



With this setup, all of the things that needed to be polled in the original design are moved to the second core while keeping all motion related items on the first core.  This eliminates most of the need for the shape generation code to poll while waiting for motion to complete.

As with most real-time operating systems, FreeRTOS allows a task to wait on an event without the need to poll for it.  In FreeRTOS, the Task Notification API provides an efficient method for a task to wait for an event to occur.  This mechanism is used in the new sand table design.  After the Shape Task completes the generation of the next target position, it calls ```xTaskNotifyWait()``` which causes the task to enter the pending state until the move completes.  For example, the code for the ```MoveTo()``` function was changed to:
```
void MoveTo(float_t x, float_t y)
{
   // Make sure we start with the servo complete flag inactive.
    xTaskNotifyStateClear(ShapeHandle);

    // Calculate the target in/out and rotary values and start moving.
    ReverseKinematics(x, y);

    // Wait until the target is reached.  Periodically check for abort.
    while ((xTaskNotifyWait(0, 0, NULL, pdMS_TO_TICKS(1000)) != pdTRUE) && !AbortShape)
    {
        // Do nothing.
    }
} // End MoveTo().
```
Note that in this implementation, we still wake up periodically to check for an abort.  The wait loop continues until ```xTaskNotifyWait()``` returns ```pdTrue```, which indicates that the move has completed, or until an abort is commanded.

When the servos reach the target position, they signal the Shape Task that the move is complete via a call to ```xTaskNotifyFromISR()``` as follows:
```
            if (RotSteps == RotStepsTo)
            {
                // Turn off the motor if it reaches the set point.
                RotOn = false;
            }
            if (InOutSteps == InOutStepsTo)
            {
                InOutOn = false;
            }
            if (!RotOn && !InOutOn)
            {
                xTaskNotifyFromISR(ShapeHandle, 0, eNoAction, &taskWoken);
            }
```
The timing of the new new motion related design is shown below: 



Again, the above diagram is greatly simplified and exaggerated.  The important points to note are:
* The timing starts with motion ISRs idle and the Shape Task generating the next move.
* At time 30, the Shape Task has completed generating the next target position and starts to pend on motion completion (i.e. it goes to sleep).
* At time 40, the ISRs see that new motion is needed, and starts moving the axes.
* At time 88, the move completes, and the ISRs notify the Shape Task.  The shape task wakes up as soon as the ISR completes.
* The Shape Task begins generating the next move.
* At time 110, the Shape Task completes its next target position calculations and starts the next move.  It then starts to pend on motion completion again.
* The cycle repeats after this.

Notice that there is still a small motion glitch with this design, but it is smaller than the original design's glitch.  The next version of the software - MySandTableFreeRTOSExp.ino - handles this.

#### Serial Logging
A new task - Print Task - was created to handle sending of all serial output.  This task resides on core 1 and uses a queue - Print Queue -  as its input.  Any task in the system, on either core, may request a message to be sent out the serial port by sending a message to the Print Queue via the ```LOG_F()``` macro.



The SerialLog2350.h file was replaced by SerialLogFreeRTOS.h and SerialLogFreeRTOS.cpp.  These files implement a new SerialLogFreeRTOS class that acts as an interface between Print Task and the rest of the system via the Print Queue.  The helper macro ```LOG_F()``` is still used, but behind the scenes it calls the ```SerialLogFreeRTOS::PrintLog()``` method to affect the serial output.  

The SerialLogFreeRTOS class contains the following methods:
* Constructor - ```SerialLogFreeRTOS(size_t bufSize, QueueHandle_t q)``` with ```bufSize``` specifying the size in bytes of the largest expected string to be output, and ```q``` specifying a queue that was already created via the FreeRTOS ```xQueueCreate()``` function.
* Destructor - ```~SerialLogFreeRTOS()``` which cleans up when a SerialLogFreeRTOS object is deleted.  The sand table software never deletes a SerialLogFreeRTOS object.
* ```PrintLog(const char *pFmt, ...)``` - Takes a printf style format string and arguments, converts them to a C string, then sends the string to the print task for outputting.

In use, the Print Task simply creates a queue, then creates a SerialLogFreeRTOS object, and waits in an infinite loop for the print queue to have a string to send out the serial port.  The entire task is as follows:
```
void PrintTask(__unused void *param)
{
    // Create our print queue and log object.
    QueueHandle_t q = xQueueCreate(PRINT_QUEUE_SIZE, sizeof(char *));
    SerialLogFreeRTOS log(MAX_LOG_STRING_SIZE * PRINT_QUEUE_SIZE, q);
    char *pData;

    // Wait to receive an outgoing message request, then send it out the serial port.
    while (1)
    {
        const uint_fast32_t PRINT_TIMEOUT_MS = 10000;
        if (xQueueReceive(q, &pData, pdMS_TO_TICKS(PRINT_TIMEOUT_MS)) == pdPASS)
        {
            Serial.print(pData);
        }
    }
} // End PrintTask().

```
The system should never directly call ```PrintLog()``` though.  Instead, the ```LOG_F()``` macro should be used.  It is defined in SerialLogFreeRTOS.h as follows:
```
#define LOG_F(level, format, ...)                                   \
    do                                                              \
    {                                                               \
        if(level)                                                   \
        {                                                           \
            SerialLogFreeRTOS::PrintLog(format , ##__VA_ARGS__);    \
        }                                                           \
    } while (0)
```

## Use Default FreeRTOSConfig.h
The FreeRTOS documentation contains a lot of information pertaining to tailoring FreeRTOSConfig.h macros to the specific system's needs.  In most cases the settings are meant to conserve memory on limited systems.  The default FreeRTOSConfig.h file for the RP2350 basically enables all features.  Since the RP2350 contains ample memory, there is no need to modify it.  Just Include FreeRTOS.h in the .ino  file and all the FreeRTOS features become available.

## Do Not Call vTaskStartScheduler()
The FreeRTOS documentation shows that a call to ```vTaskStartScheduler()``` is required after tasks are created in  order to start the scheduler.  However, for the RP2350 version, this is unnecessary since, I assume, that the scheduler is started automatically upon exit from ```setup()```.  It was found that when an explicit call to  ```vTaskStartScheduler()```  was added at the end of ```setup()```, the system crashed. **BEWARE:  DO NOT CALL ```vTaskStartScheduler()``` WHEN USING THE RP2350.**

## Debug / Safety Net Code
When using FreeRTOS, it is easy to make a coding mistake that will cause the system to crash in such a way that you can no longer download to the RP2350 board.  I found this out the hard way and had to go through the factory reset procedure.  The procedure is not difficult, but  due to the need to simultaneously activate 2 push buttons on the board, and the physical placement of the board in the sand table, this was something I didn't want to repeat.  To handle this, the code below was added in ```setup()```.  It waits until the speed pot is not zero.  I would recommend a similar setup to anyone experimenting with FreeRTOS.
```
    // Special code for use while debugging.  Hold startup until the speed pot
    // is no longer in the pausing state.  If something we did caused FreeRTOS
    // to go into the weeds, this will allow our USB connection to be seen by
    // the host computer and allow us to recover.
    while (ReadAPot(SPEED_POT_PIN) <= KNOB_MIN_VAL + 16) { /* Do nothing.*/ }
```

## loop() Priority 4
The new sand table design did not need to use the ```loop()``` function since its main loop is executed in the Shape Task.   However, it was found that the ```loop()``` function must be defined.  The sand table ```loop()``` function simply contains a delay to allow the idle task to execute. It was also found that the ```loop()``` executes at priority 4.

## Add Volatile
Since the system was partitioned into separate concurrently executing tasks, several of the global variables needed to be assigned as ```volatile```.  Among these changes were:
```
volatile bool         Pausing      = false;  // 'true' when pausing.
volatile bool         AbortShape   = false;  // 'true' if aborting ghe current shape.
volatile bool         RandomSeedChanged = false;  // 'true' when random seed has been changed.
```

## Critical Section Handling
A few sections of code needed protection to insure that several lines of code were performed atomically without being preempted by ISRs or other tasks.  Previously, the ```noInterrupts()``` and ```interrupts()``` functions were used for this.  However, for FreeRTOS, the ```taskENTER_CRITICAL()``` and ```taskEXIT_CRITICAL()``` functions are used to do the same thing.  Most cases where critical sections are needed are to start both servos at the same time.  For example:
```
    // Start the move by turning the motors on atomically.
    taskENTER_CRITICAL();
    RotOn   = true;
    InOutOn = true;
    taskEXIT_CRITICAL();
``` 
Other places include handling some of the remote commands.  In addition, several functions in the sand table software use the ```delayMicroseconds()``` function to generate short execution delays.  It was found that these delays were not very accurate under FreeRTOS.  Protecting these calls via critical sections seemed to fix the problem.  For example:
```
        taskENTER_CRITICAL();
        InOutStepper.Step(DirInOut);
        delayMicroseconds(delay);
        taskEXIT_CRITICAL();
```

## Random Seed Setup
The ```randomSeed()``` function is used to initialize the random number generator to a specific value.  At startup, the sand table code generates a random seed and feeds it to ```randomSeed()```.  It was found that when ```randomSeed()``` was called from ```setup()``` its new value was not reflected in the Shape Task.  It is known that some of the Arduino libraries do not work well with FreeRTOS, and the random number generator is one of them.  My conjecture is that each task has its own random number seed.  My workaround was to move the setting of the random number seed to the start of the Shape Task since this is the only task that uses random numbers.

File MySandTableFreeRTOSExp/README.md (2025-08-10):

Upgrading RP2350 Based Sand Table to FreeRTOS
===
Sand Table

This document describes the firmware design and code changes that were made to the [RP2350 FreeRTOS based Sand Table](https://github.com/regnaDkciN/SandTable/tree/main/MySandTableFreeRTOS) to queue motion moves ahead of execution.  Major changes also include an improved method of randomly selecting the next shape to draw based on weighted probabilities.  The new version -  [MySandTableFreeRTOSExp](https://github.com/regnaDkciN/SandTable/tree/main/MySandTableFreeRTOSExp) - was so named because it was initially an experimental version, but has become stable and the name just stuck.

## Motivation
The FreeRTOS version of the sand table software went a long way to improve motion smoothness.  However, some motion glitches were still possible due to the time it takes to calculate the next move.  This new version adds pre-execution motion planning and queueing which goes further in removing motion glitches. 

## The Problem
As explained in the MySandTableFreeRTOS version, move calculations can take up enough time to cause glitches as seen in the timing diagram below:



The important points to note are:
* The timing starts with motion ISRs idle and the Shape Task generating the next move.
* At time 30, the Shape Task has completed generating the next target position and starts to pend on motion completion (i.e. it goes to sleep).
* At time 40, the ISRs see that new motion is needed, and starts moving the axes.
* At time 88, the move completes, and the ISRs notify the Shape Task.  The shape task wakes up as soon as the ISR completes.
* The Shape Task begins generating the next move.
* At time 110, the Shape Task completes its next target position calculations and starts the next move.  It then starts to pend on motion completion again.
* The cycle repeats after this.
* A motion glitch occurs when the ISRs are idle at time 100.

If motion generation calculations could be calculated ahead of time, this glitch could be removed.

## New Design
The diagram below attempts to show the most important parts of the old design's motion related code structure:



Execution proceeds as follows:
1. A shape function calculates the next X,Y position of the shape and calls ```GotoXY()``` with the new position.
2. ```GotoXY()``` loops, breaking the move into smaller segments, basically interpolating between the current position and the new segment position.  It calls ```MoveTo()``` with the new segment position.
3. ```MoveTo()``` calls ```ReverseKinematics()``` with the new segment position, then goes to sleep waiting on the move to complete.
4. ```ReverseKinematics()``` generates the servo positions corresponding to the new segment X,Y coordinates.  It then starts the move and returns to ```MoveTo()```.
5. The ISRs repeatedly execute, moving the axes to the new position.  When the move completes, the ISRs signal the Shape Task which wakes up, completing ```MoveTo()```'s execution.
6. ```MoveTo()``` returns to ```GotoXY()```, which returns to the original shape function, and the process repeats.

In order to improve the motion performance, the Shape Task has been split into two tasks and a new Motion Queue has been added:



* The new Shape Task contains the code to calculate moves and queues the new position data to the new Motion Queuel Task.  The Shape Task still executes on core 0 at priority 5.
* The new Servo Control Task takes moves off the Motion Queue and sends them to the servo ISRs for execution.  It executes on core 0 at priority 6.
* The new Motion Queue holds a limited number of ```PlannerData``` structures.  The ```PlannerData``` structure holds the target steps for each servo:
	```
	// PlannerData structure.  Used to pass data between the planner and the
	// servo controller task.
	struct PlannerData
	{
	    int_fast32_t m_InOutStepsTo;    // In/out target steps for move.
	    int_fast32_t m_RotStepsTo;      // Rotary target steps for move.
	};
	
	```
	
*Note that ```MotorRatios()``` moves are handled differently from normal moves since they are not really planned, and are mainly handled in the ISRs.  The Servo Control Task does not participate in ```MotorRatios()``` moves.*

To help further understand the new design, compare the following new design diagram to the old design diagram above:



Execution of the new design proceeds as follows:
1. Just as before, a shape function calculates the next X,Y position of the shape and calls ```GotoXY()``` with the new position.
2. Just as before, ```GotoXY()``` breaks the move into smaller segments, basically interpolating between the current position and the new segment position. However, unlike before, ```GotoXY()``` calls ```ReverseKinematics()``` with the new segment position.
3. ```ReverseKinematics()``` generates the servo position based on the new segment X,Y position.  It then attempts to send the new servo position to the Motion Queue via a call to ```xQueueSend()```.  If the Motion Queue is already full, the task goes to sleep waiting for space to free up on the Motion Queue. 
4. When space becomes available on the Motion Queue, ```ReverseKinematics()``` saves the new servo position on the queue and immediately returns to ```GotoXY()```.  
5. Concurrently with items 1 through 4, the Servo Control Task is waiting for the Motion Queue to become non-empty via a call to ```xQueueReceive()```.
6. Once a new servo position is fetched from the Motion Queue, the Servo Control Task starts the move and begins waiting for the move to complete (it goes to sleep waiting) via a call to ```xTaskNotifyWait()```.
7. As soon as motion completes, the ISRs wake the waiting Servo Control Task via a call to ```xTaskNotifyFromISR()```.
8. The process repeats.

Note that this new design allows several moves to be calculated ahead of time, which allows the Servo Control Task start new moves immediately after completion of the preceding move.  This minimizes the possibility of generating a motion glitch due to lengthy  position calculations.

## Other Motion Related Code Changes

### New Variables
Several new global variables were needed.  These include task and queue handles and new working versions of some of the motion variables.  The new variables include:
```
// RTOS related variables.
TaskHandle_t      ServoCtrlHandle    = NULL;    // Handle for servo control task.
TaskHandle_t      ShapeHandle        = NULL;    // Handle for shape task.
QueueHandle_t     PlannerQueueHandle = 0;       // Handle for planner queue.
const UBaseType_t PLANNER_Q_LENGTH   = 20;      // Num entries in planner queue.
volatile float_t  PlannerCurrentX    = 0.0;     // Planned location of ball (X).
volatile float_t  PlannerCurrentY    = 0.0;     // Planned location of ball (Y).
volatile bool     MoveInProcess      = false;   // True if moves are in process.
```

### GotoXY()
The new version of ```GotoXY()``` uses working values for the current X,Y position rather than actual current values:
```
volatile float_t  PlannerCurrentX;     // Planned location of ball (X).
volatile float_t  PlannerCurrentY;     // Planned location of ball (Y).
```

 These working values are based on the final position of the previously queued move.  This way, ```GotoXY()``` can plan ahead based on the expected starting position instead of the current actual position.  In order to keep the working values current, they are updated in ```StartShape()```, which is called before starting each shape position calculation.  Just to be safe, they are also updated at the end of each shape, after all movement has completed, in ```EndShape()```.

### HandleRemoteCommandsTask() Changes
The commands that cause the current motion to abort ('R' and 'N') added code to reset the Motion Queue via a call to ```xQueueReset()```.  This insures that the current motion will stop immediately.

### RotateToAngle()
The ```RotateToAngle()``` function rotates the rotary axis to a specified angle from the origin leaving the in/out arm position unchanged.  Unlike ```ForceInOut()``` and ```ForceRot()```, this function generates a coordinated move.  However, it is more like ```MotorRatios()``` in that it bypasses

### WaitForMoveComplete()
A new function - ```WaitForMoveComplete()``` was added to wait for the last move of a shape to complete before continuing on.  This was necessary due to the addition of the Motion Queue.  Shapes must fully complete execution, including finishing all queued moves, before the shape is considered to be complete.  ```WaitForMoveComplete()``` is called from a few places in the code that are not strictly considered as being the end of a shape.  These places include any place that ```GotoXY()``` is called, but not as part of a shape.  For example, the code for ```ExtendInOut()``` is now the following:
```
void ExtendInOut()
{
    GotoXY(MAX_SCALE_F * cosf(RadAngle), MAX_SCALE_F * sinf(RadAngle));
    WaitForMoveComplete();
} // End ExtendInOut().
```

## Weighted Random Numbers
This shape selection logic was replaced by a new class - ```RandomVoseAlias``` - that provides for efficient sampling of random values from a discrete probability distribution.  For a complete writeup on the alias method, including the intuition and important proofs, please see the article ["Darts, Dice, and Coins: Sampling from a Discrete Distribution"](http://www.keithschwarz.com/darts-dice-coins/).

### ShapeInfo Class Changes
The old version of the sand table software used a clunky means of selecting the next random shape.  It would tentatively select a random shape, then check to see if the shape had been executed recently.  If so, it would select a new random shape, and repeat the process until a suitable shape was found.  The ```ShapeInfo``` class contained a ```m_Delay``` value that was used to determine the number of cycles that must elapse between consecutive generation of each shape was allowed.  The class also contained logic to remember the cycle at which the last execution of each shape took place.

The new version replaces the ```m_Delay``` member with the ```m_Weight``` member.  It represents the probabilistic weight of this object.  It is used to generate a weighted probabilities vector which is used to randomly select shapes for execution.  A higher value causes the shape to be selected more frequently.  For more info see the Random Shapes section below.

The ```MakeShape()``` method also changed to simply call the associated shape function, and keep some statistics.

### RandomShapes[] Table
The weight value of each entry of the ```RandomShapes[]``` table is  based on how often each shape should execute based on how often a ```RandomWipe``` should be executed.  For example the code below shows that:
- ```RandomPlot``` should execute 2 times as often as ```RandomWipe```.
- ```RandomLines``` should execute 3 times as often as ```RandomWipe```.
- ```RandomSuperStar``` should execute 10 times as often as ```RandomWipe```.
- And so on...
```
ShapeInfo RandomShapes[] =
{
    ShapeInfo("RandomWipe", RandomWipe, 1),
    ShapeInfo("RandomPlot", RandomPlot, 2),
    ShapeInfo("RandomLines", RandomLines, 3),
    ShapeInfo("RandomSuperStar", RandomSuperStar, 10),
    ShapeInfo("EllipseSeries", EllipseSeries, 10),
    ShapeInfo("RandomCircle", RandomCircle, 12),
    ShapeInfo("HeartSeries", HeartSeries, 15),
    ShapeInfo("RandomSpirographWithSquare", RandomSpirographWithSquare, 20),
    ShapeInfo("RandomSpirograph2", RandomSpirograph2, 25),
    ShapeInfo("RandomRose", RandomRose, 25),
    ShapeInfo("RandomClover", RandomClover, 25),
    ShapeInfo("RandomRatios", RandomRatios, 30),
    ShapeInfo("RandomSpirograph", RandomSpirograph, 30),
    ShapeInfo("PolygonSeries", PolygonSeries, 30),
    ShapeInfo("StarSeries", StarSeries, 30),
    ShapeInfo("RandomRatiosRing", RandomRatiosRing, 30)
}; // End RandomShapes[].
```

### InitProbabilities()
A new function - ```InitProbabilities()``` -  was added to initialize the weighted probabilities for each entry of the ```RandomShapes[]``` table.  It steps through the entries of the ```RandomShapes[]``` table and sums their weights.  It then creates a probability vector of associated shape probability via dividing each entry weight by the total weight.  It then initializes the weighted probability random shape generator via a call to ``` WeightedRandom.Init()```.  Global variables used for weighted random shape generation are:
```
// Create a weighted random object for use in selecting the next shape to execute.
RandomVoseAlias WeightedRandom;
// Vector of weighted probabilities used with WeightedRandom.
std::vector<float_t> Probabilities;
```

### GenerateRandomShape()
The ```GenerateRandomShape()``` function was simplified to select a new random shape and execute it. Its has simplified to the following:
```
void GenerateRandomShape()
{
    // Execute a random shape.
    RandomShapes[WeightedRandom.Next()].MakeShape(ShapeIteration);

    // Increment the iteration count since we just executed something.
    ShapeIteration++;
} // End GenerateRandomShape();
```

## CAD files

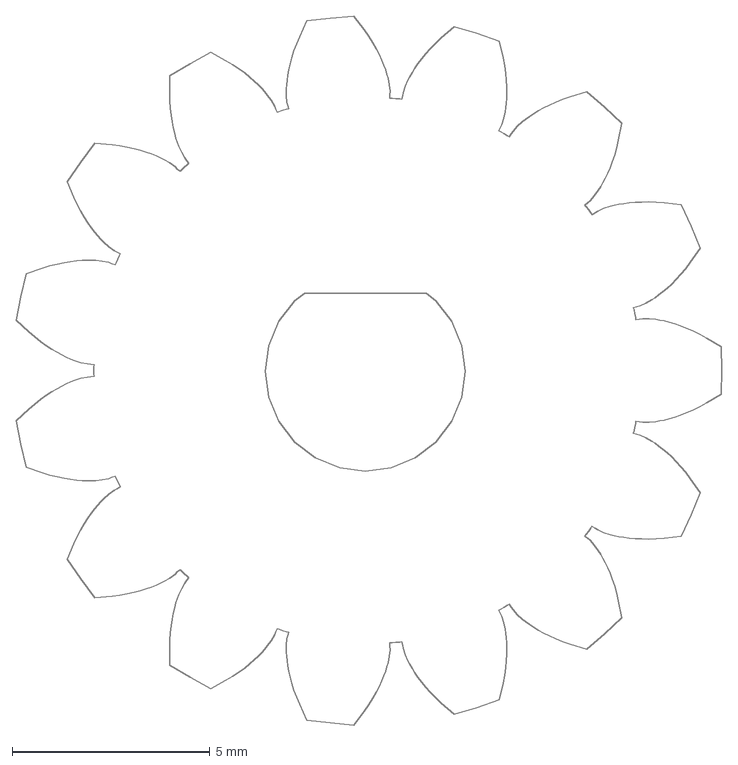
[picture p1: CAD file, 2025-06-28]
3D Printed Parts/Gear Hole Test 1.10.dxf
17.9 x 17.9 mm

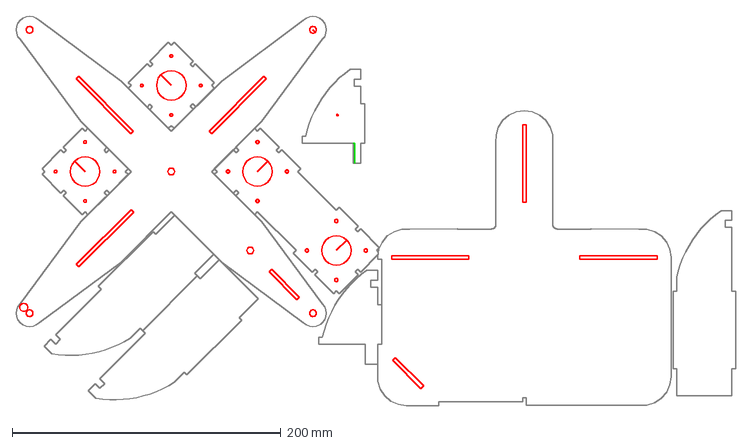
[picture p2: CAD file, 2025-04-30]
Laser Cut Parts/Base.dxf
535.1 x 289.4 mm

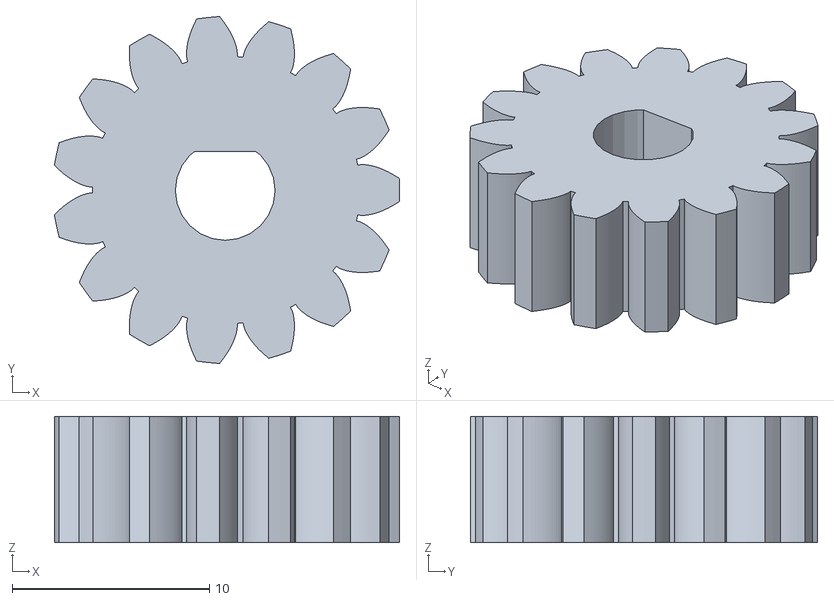
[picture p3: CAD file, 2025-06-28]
3D Printed Parts/Thick Small Gear.stl
17.5 x 17.6 x 6.40

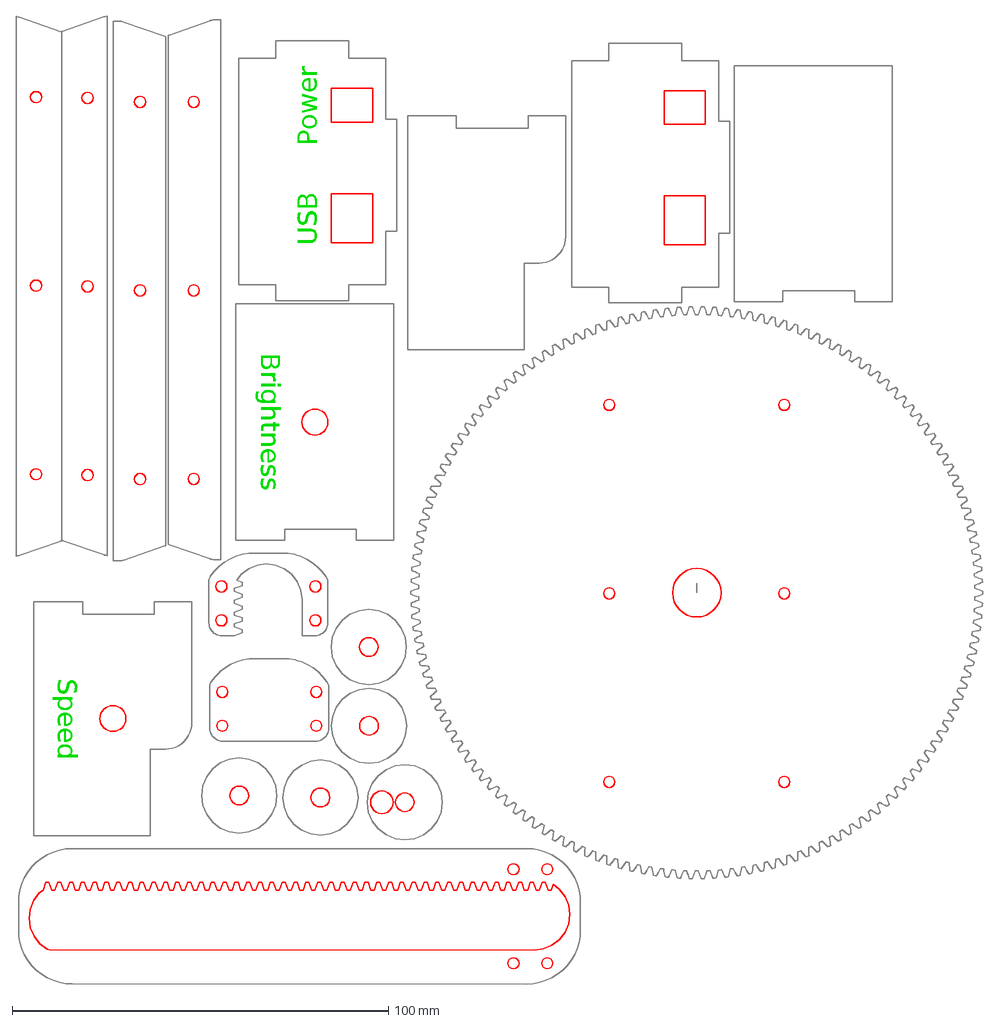
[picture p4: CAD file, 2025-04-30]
Laser Cut Parts/Modified Parts.dxf
Power
USB
Brightness
Speed

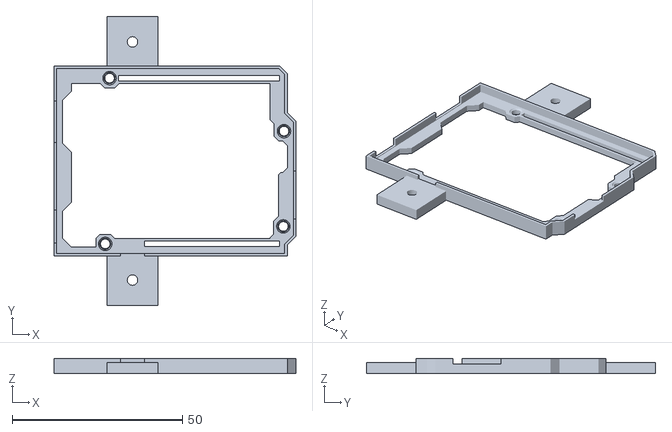
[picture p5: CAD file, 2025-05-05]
3D Printed Parts/Metro_2350_Bumper.stl
71.2 x 85.0 x 4.48

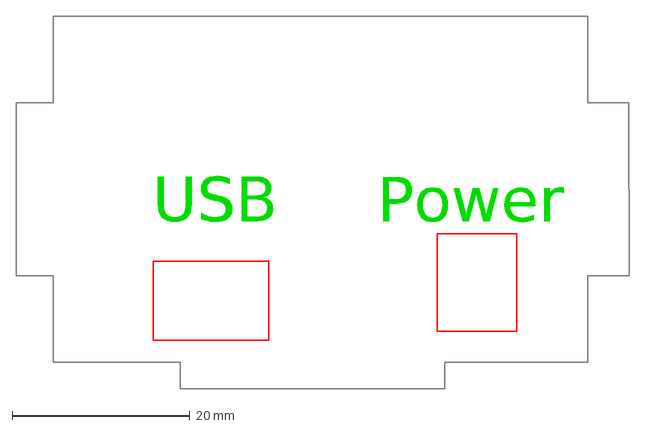
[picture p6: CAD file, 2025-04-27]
Laser Cut Parts/Faceplate 2350.dxf
Power
USB

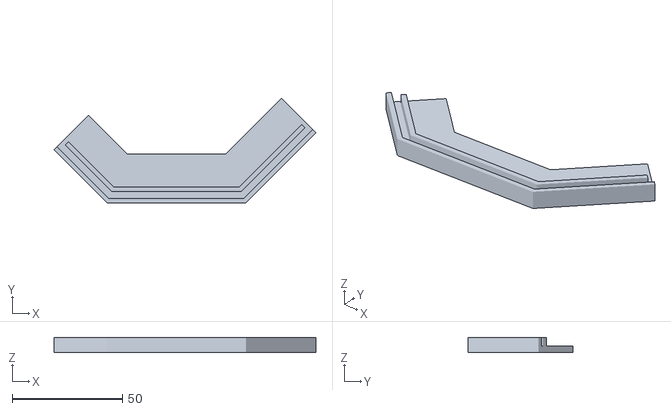
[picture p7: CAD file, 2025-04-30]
3D Printed Parts/Bezel3.stl
118.9 x 47.5 x 7.00

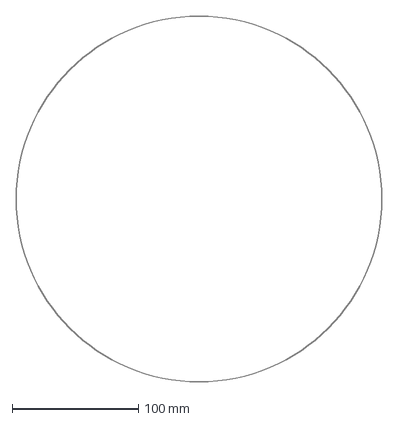
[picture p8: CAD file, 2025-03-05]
Laser Cut Parts/Window.dxf
290.0 x 290.0 mm

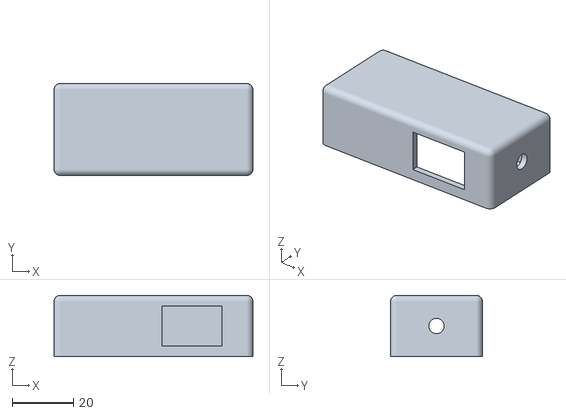
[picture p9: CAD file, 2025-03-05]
3D Printed Parts/Power Box.stl
65.0 x 30.0 x 20.0

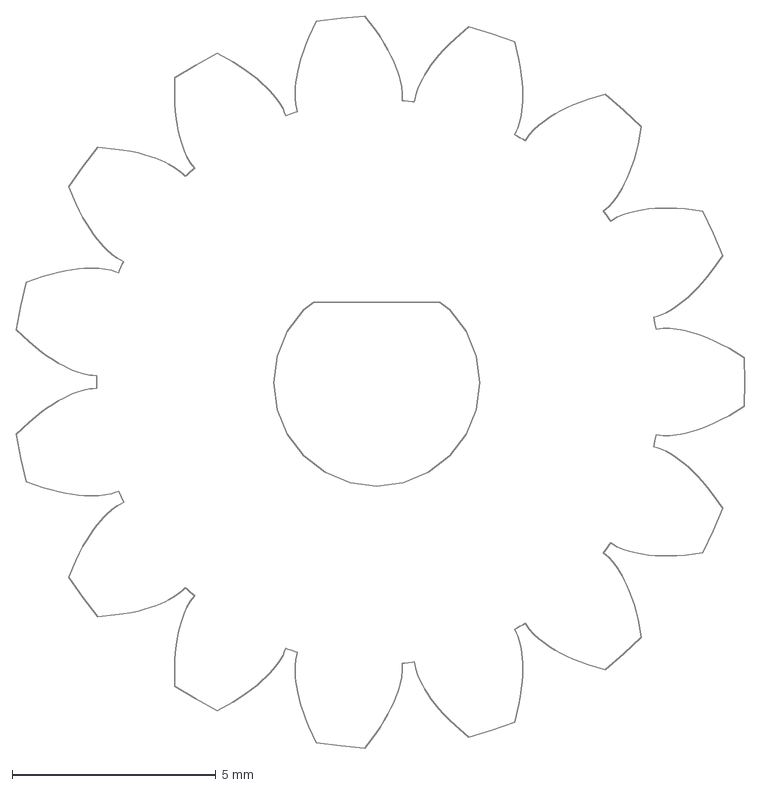
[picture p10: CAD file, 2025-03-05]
Laser Cut Parts/Gear Hole Test 1.10.dxf
17.9 x 17.9 mm

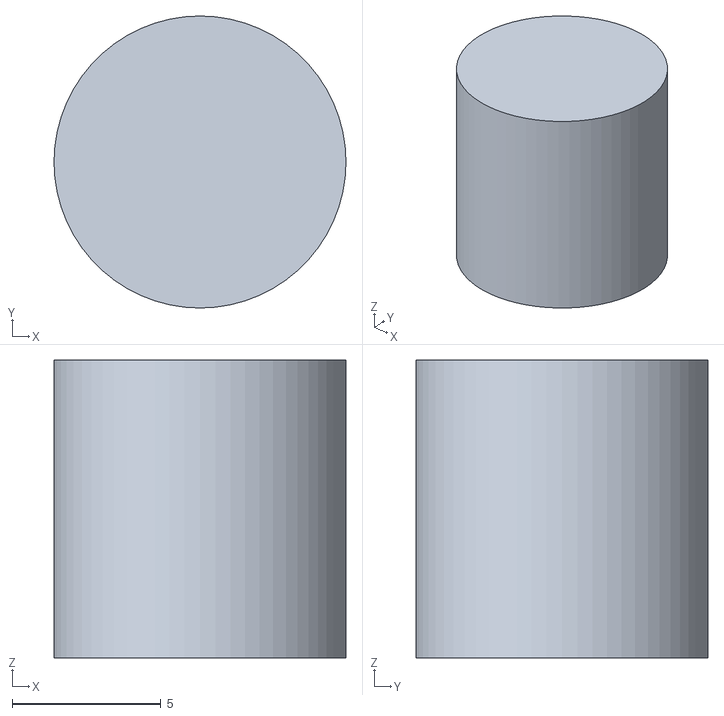
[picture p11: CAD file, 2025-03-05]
3D Printed Parts/Window Knob.stl
9.80 x 9.80 x 10.0

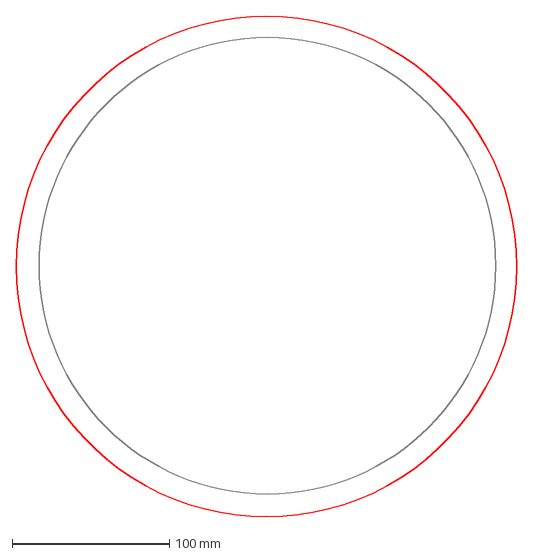
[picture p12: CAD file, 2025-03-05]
Laser Cut Parts/Window Holder no Text.dxf
318.0 x 318.0 mm

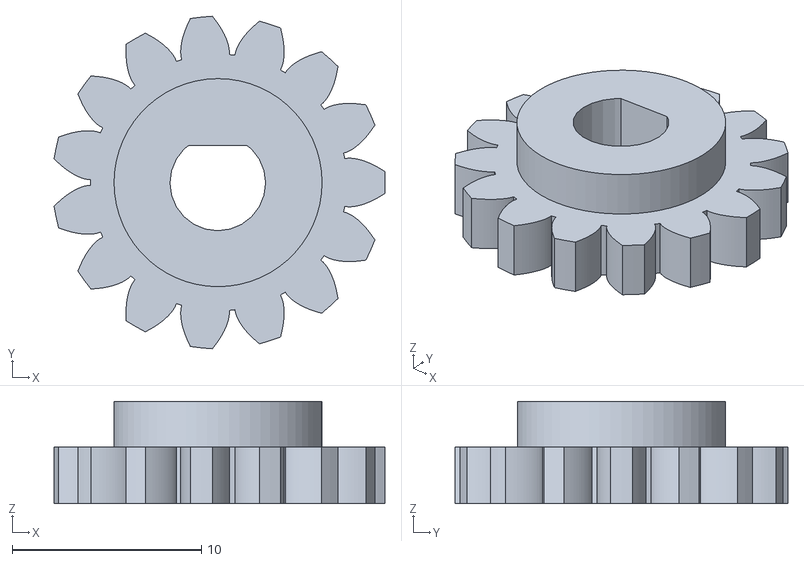
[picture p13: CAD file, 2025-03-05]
3D Printed Parts/Small Gear With Bushing.stl
17.5 x 17.6 x 5.40

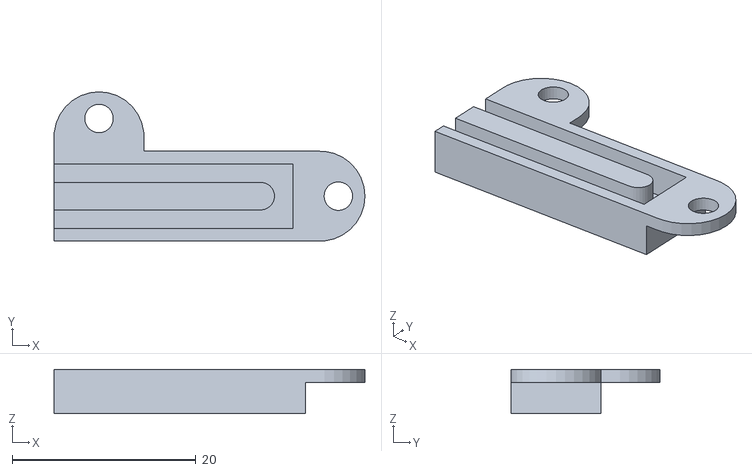
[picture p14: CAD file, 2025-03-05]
3D Printed Parts/Reed Switch Mount.stl
33.8 x 16.2 x 4.80

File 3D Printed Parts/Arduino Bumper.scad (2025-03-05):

// OpenSCAD script to modify the original Arduino Bumper as follows:
//   - Enlarge in the X and Y axes to fit a slightly larger board.
//   - Shrink in the Z direction based on the current project need.
//   - Shrink the diameter of the mounting holes so that M3 screws will thread
//     directly into them rather than passing through.


XScale           = 1.01;        // X axis scale for entire assembly.
YScale           = XScale;      // Y axis scale for entire assembly.
ZScale           = 1.0;         // Z axis scale for entire assembly.
SmallHoleD       = 2.8;         // Diameter of (shrunken) mounting holes.
OrigThickness    = 2.6;         // Thickness of original assembly.
DesiredThickness = 2.0;         // Final thickness of the assembly.
MountSize        = 15.0;        // Length of mount cube sides.
MountThickness   = 3.2;         // Thickness of side mounts.
MountHoleD       = 3.1;         // Diameter of side mount holes.
HoleThickness    = DesiredThickness - 0.8;
                            // Thickness of new (shrunken) mounting holes.
AlignHoles    = false;      // Set true to add center alignment pins.
                            // Be sure to set to false before final render.


MountingHoleCoords =        // X/Y coordinates of the 4 mounting holes.
            [[31.74, 8.70], [31.55, -19.05], [-19.05, 24.12], [-20.30, -24.12]];


module AlignmentPin()
{
    cylinder(d = 0.1, h = 5.0, $fn = 30);
}

// Import the original model, and display mounting hole alignment centers if requested.
module Original()
{
    import("Arduino_Bumper_0006.stl", convexity = 10);
    // Display the mountinng hole centers for alignment purposes if requested.
    if (AlignHoles)
    {
        for (c = MountingHoleCoords)
        {
            translate([c.x, c.y, 0.0]) AlignmentPin();
        }
    }
}


// Scale the original assembly.
module ScaledOriginal(s = [1.0, 1.0, 1.0])
{
    difference()
    {
        translate([0.0, 0.0, -(OrigThickness - DesiredThickness)]) scale(s) Original();
        translate([0.0, 0.0, -5]) cube([100.0, 100.0, 10.0], center = true);
    }
}


// A cube containing the (shrunken) mounting hole.  Adds alignment centers if desired.
module Hole()
{
    // Create a small cube with a shrunken mounting hole.
    difference()
    {
        translate([0.0, 0.0, HoleThickness / 2 + .4]) 
            cube([4.0, 4.0, HoleThickness], center = true);
        translate([0.0, 0.0, -1.1]) cylinder(d = SmallHoleD, h = 4.0, $fn = 30);
    }
    // Display the mountinng hole centers for alignment purposes if requested.
    if (AlignHoles)
    {
        translate([0.0, 0.0, 1.0]) AlignmentPin();
    }
}


// A side mount containing a mounting hole.
module Mount()
{
    difference()
    {
        // The mounting cube.
        cube([MountSize, MountSize, MountThickness]);
        // The mounting hole.
        translate([MountSize / 2, MountSize / 2, -1])
            cylinder(d = MountHoleD, h = MountThickness + 2.0, $fn = 30);
    }
}


// Final assembly with possibly enlarged X and Y axes and shrunken Z axis and mounting holes.
module FinalAssembly(s = [1.0, 1.0, 1.0])
{
    ScaledOriginal(s);
    for (c = MountingHoleCoords)
    {
        #translate([c.x * XScale, c.y * YScale, 0.0]) Hole();
    }
    
    // Add side mounts.
    translate([-20.0, -27.5 - MountSize, 0.0]) Mount();
    translate([-20.0,  27.5, 0.0]) Mount();
}

FinalAssembly([XScale, YScale, ZScale]);

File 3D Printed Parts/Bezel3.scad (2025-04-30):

BaseHeight = 3;
RailLipHeight = 4;
RailLipWidth = 2;
RailSlotWidth = 3.2;
RailWidth = RailSlotWidth + RailLipWidth * 2;
RailHeight = BaseHeight + RailLipHeight;
BaseDepth = RailWidth + 15;
WingAngle = 135;
LeftRailLength = 45;
RightRailLength = 34;
CentralRailLength = 63;
fudge = 0.02;

module Rail(length)
{
    cube([length, BaseDepth, BaseHeight]);
    difference()
    {
        cube([length, RailWidth, RailHeight]);
        translate([-.5, RailLipWidth, BaseHeight])
            cube([length + 1, RailSlotWidth, RailHeight]);
        translate([-fudge / 2, RailLipWidth + RailSlotWidth - fudge, BaseHeight])
            cube([RailLipWidth + fudge, RailLipWidth + fudge, RailHeight]);
        translate([length - RailLipWidth - fudge / 2, 
                    RailLipWidth + RailSlotWidth - fudge / 2, 
                    BaseHeight])
            cube([RailLipWidth + fudge, RailLipWidth + fudge, RailHeight]);
    }
}

module Rails()
{
    Rail(CentralRailLength);
    
    rotate([0, 0, WingAngle + 180]) 
        translate([-RightRailLength, 0, 0]) Rail(RightRailLength);    
    
    translate([CentralRailLength, 0, 0]) rotate([0, 0, 180 - WingAngle])
        Rail(LeftRailLength);   
}

//Base(60);
Rails();

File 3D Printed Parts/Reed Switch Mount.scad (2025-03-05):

ReedLen = 16;
ReedWid = 2;
ReedAndWireLen = ReedLen + 10;
ReedAndWireWid = 10;
NubDia = 3;
Margin = 1.4;
BoxWid = 2 * ReedWid + 2 * Margin + NubDia;
BoxLen = ReedAndWireLen + Margin;
BoxH = ReedWid + 2 * Margin;
WireWid = 1.5;
MountHoleD = 3.1;         // Diameter of side mount holes.

echo(BoxWid);

module Box()
{
    difference()
    {
        // Basic box.
        cube([BoxLen, BoxWid, BoxH], center = true);

        //  Cut out space for the reed soitch and one of its leads.
        translate([-Margin, (NubDia + ReedWid) / 2, Margin]) 
            cube([BoxLen, ReedWid, BoxH], center = true);
        translate([-Margin, -(NubDia + ReedWid) / 2, Margin])
            cube([BoxLen, ReedWid, BoxH], center = true);
            
        // Add space for the rounded off the upper wire guide.  
        translate([(BoxLen - (ReedWid + NubDia / 2)) / 2 - Margin, 0, Margin]) 
            cube([ReedWid + NubDia / 2, NubDia + .01, BoxH], center = true);
    }

    // Round off the upper wire guide.
    translate([(BoxLen - NubDia) / 2 - Margin - ReedWid, 0, -BoxH / 2]) 
        cylinder(d = NubDia, h = BoxH, $fn = 30);
}

module Tab()
{
    difference()
    {
        // Create the tab circlw.
        cylinder(d = BoxWid, h = Margin, $fn = 30);
        
        // Cut off half of the tab to make a semicircle.
        translate([0, -BoxWid, -.01])
            cube([BoxWid * 2, BoxWid * 2, BoxH]);
            
        // Cut out the mounting hole.
        translate([-2, 0, -.01])
            cylinder(d = MountHoleD, h = BoxH, $fn = 30);
    }
    
    // Extend the tab to allow room for the mounting screw head.
    translate([0, -BoxWid / 2, 0]) 
        cube([MountHoleD / 2, BoxWid, Margin]);
}

module ReedSwitchMount()
{
    // Start with the basic box.
    Box();
    
    // Add the mounting tabs.
    translate([-(BoxLen - BoxWid) / 2, (BoxWid + MountHoleD) / 2, BoxH / 2 - Margin])
        rotate([0, 0, -90]) Tab();
    translate([(BoxLen + MountHoleD)/ 2, 0, BoxH / 2 - Margin])
        rotate([0, 0, 180]) Tab();
}

ReedSwitchMount();

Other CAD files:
3D Printed Parts/Arduino_Bumper_0006.stl
3D Printed Parts/Arduino Bumper.stl
3D Printed Parts/Power Box Lid.stl
3D Printed Parts/Metro_2350_Bumper.scad
3D Printed Parts/Small Gear With Bushing.scad
3D Printed Parts/Thick Small Gear.scad

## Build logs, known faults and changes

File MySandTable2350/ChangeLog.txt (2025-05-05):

Arduino UNO to Adafruit Metro 2350 Sand Table Changes
=====================================================

- Data type changes:
    + Since UNO was tight on space, all data types were declared as the smallest
      size that would do the job.  Generally (u)int16_t.  But the 2530 has lots
      of memory (compared to the UNO), so size is unimportant.  Speed is a 
      higher priority.  As a result, almost all data types were changed fast
      types.  For example, uint16_6 becomes uint_fast16_t, etc.
- Speed delay value changes:
    + The UNO timer clock period was set up to 4 uSed.  The 2350 timer clock
      runs at 1 uSec.  To account for this, all speed delay values were multiplied
      by 4.  For example SPEED_DELAY_MIN_VAL was changed from 25 on the UNO to
      100 on the 2350, etc.
- Different ISR handling.
    + The UNO needs to setup the timer clock rate before use:
        TCCR1A = 0;           // Init Timer1A (for rotation motor).
        TCCR1B = 0;           // Init Timer1B (for in/out motor).

        TCCR1B |= B00000011;  // Prescaler = 64. (4 microsecond tick).
        OCR1A = 1000;         // Timer Compare1A Register.
        OCR1B = 1000;         // Timer Compare1B Register.

        TIMSK1 |= B00000110;  // Only use one interupt.
        
      The 2350 already has its timer running at 1MHz.
    + The UNO used a simple interrupt setup with "ISR(vector)" indicating that
      a timer interrupt exists, and heads the interrupt handler itself.
      
        ISR(TIMER1_COMPA_vect)
        {
            OCR1A = TCNT1 + RotDelay;    
            ISR code            
        }
        ISR(TIMER1_COMPB_vect)
        {
            OCR1B = TCNT1 + InOutDelay;
            ISR code
        }

      The 2350 handles timer interrupts more normally in that the ISR must be declared
      before use, and added to the timer list before it can be used.
      
        int64_t RotaryServoIsr(__unused alarm_id_t id, __unused void *user_data);
        int64_t InOutServoIsr(__unused alarm_id_t id, __unused void *user_data);
        
        add_alarm_in_us(1000000, RotaryServoIsr, NULL, false);
        add_alarm_in_us(1000000, InOutServoIsr,  NULL, false);
        
        int64_t RotaryServoIsr(__unused alarm_id_t id, __unused void *user_data)
        {
            ISR code
            return -RotDelay;
        }
        int64_t InOutServoIsr(__unused alarm_id_t id, __unused void *user_data)
        {
            ISR code
            return -InOutDelay;
        }
    + In order for interrupt to repeat, the UNO bumps the corresponding OCR1x 
      register at the start of each ISR. as shown above.  The 2350 returns
      the delay value from its ISR as a negative value, indicating that the next
      tick should occur exactly that many microseconds after the time the current 
      ISR triggered.
- Speed increments/decrements in HandleRemoteCommands() are adjusted by a factor
  of 4 to account for the timer speed differences noted above.
- The UNO used an unused analog input and a function - GenerateRandomSeed() - to
  generate a random seed at startup.  The 2350 has a hardware true random number
  generator with a standard function - get_rand_32() - to generate a 32-bit
  random number.  So GenerateRandomSeed() was removed for the 2350.
- UNO supplies a squaref() function to square a float value.  The 2350 supplies
  a function named sq() that does the same thing. So uses of squaref() were
  changed to sq().
- The rotary servo ISR contains logic to generate compensation pulses in the
  inout servo based on rotary motion.  Part of this logic uses a short delay
  to affect a pulse on the inout servo.  In the UNO, a pulse delay of 1 microsecond
  was used.  However, since the 2350 is so much faster, the pulse delay was 
  changed to 5 microseconds.
- The 2350 includes an SD card holder and a power switch that the UNO doesn't have.
  Both of these are mounted on edges of the card.  To accommodate these devices,
  the mounting bumper was modified to add notches in the appropriate spots.
- Note that the UNO firmware uses D12 as the enable for the rotation axis.  On the 
  2350, this pin is used for other purposes, and is not brought out to a header
  pin.  In its place, D22 is brought out on the 2350.  As a result, the 2350 
  code was changed to initialize D22 as an output, and remapped the enable to
  use D22 instead.
- SerialLog changes. Removed LOG_U() macro, and replaced all serial logging with
  LOG_F() calls that use printf() style handling.
- Faceplate USB hole needs to be lowered by 2mm and height reduced to 10mm.
- Temporarily changed all floats and float operations to doubles to work around a
  2350 FPU compiler issue #2429:
     https://github.com/raspberrypi/pico-sdk/pull/2429
  The issue has been fixed on the development branch, but not added to the release
  branch yet.  When it is released, this sand table code will restore operation
  with floats, as double precision is not needed.  Will change the following back
  when compiler FP fix is released:
    double -> float_t
    cos    -> cosf
    sin    -> sinf
    hypot  -> hypotf
    atan2  -> atan2f
    round  -> roundf
    trunc  -> truncf
    sqrt   -> sqrtf
    pow    -> powf
- Arduino UNO is a 5V device. 2350 is 3.3V.  Changed the pot voltage from the CNC
  shield 5V output to its 3.3V output (next to the RST pin).
- The MOSFET used for the UNO version (IRFZ44N) has a Gate Threshold Voltage
  (VGS) of 2-4 volts.  This is a little too high for the 3.3V 2350 and did
  not fully turn on.  Replaced the IRFZ44N with IRLZ44N 
    https://www.amazon.com/dp/B0CBKH4XGL
  which has a VGS of 1-2 volts.  This allowed the MOSFET to turn on fully.  
  Also added a 100K resistor between the gate and source to keep the MOSFET from
  conducting at power-up.
- Found a lot of noise on the 2350 analog inputs.  This showd up as LED flicker
  at lower brightnesses.  To compensate for this, the pot readings (analog inputs)
  were configured with a resolution of 12 bits, then shifted right by 4 bits after
  reading.  This effectively produced an 8 bit resolution, which is fine for the
  sand table application, but eliminated the noise/flicker issue.
- Also changed the PWM (LED) output frequency to 100,000 to help reduce flicker.
- Not 2350 related, but added LED update while homing.

2350 picture link:
    https://cdn-shop.adafruit.com/230x173/6003-10.jpg
UNO picture link:
    https://cdn-shop.adafruit.com/230x173/4806-05.jpg

Upgrading from Arduino UNO to Adafruit Metro 2350 (A Case Study)

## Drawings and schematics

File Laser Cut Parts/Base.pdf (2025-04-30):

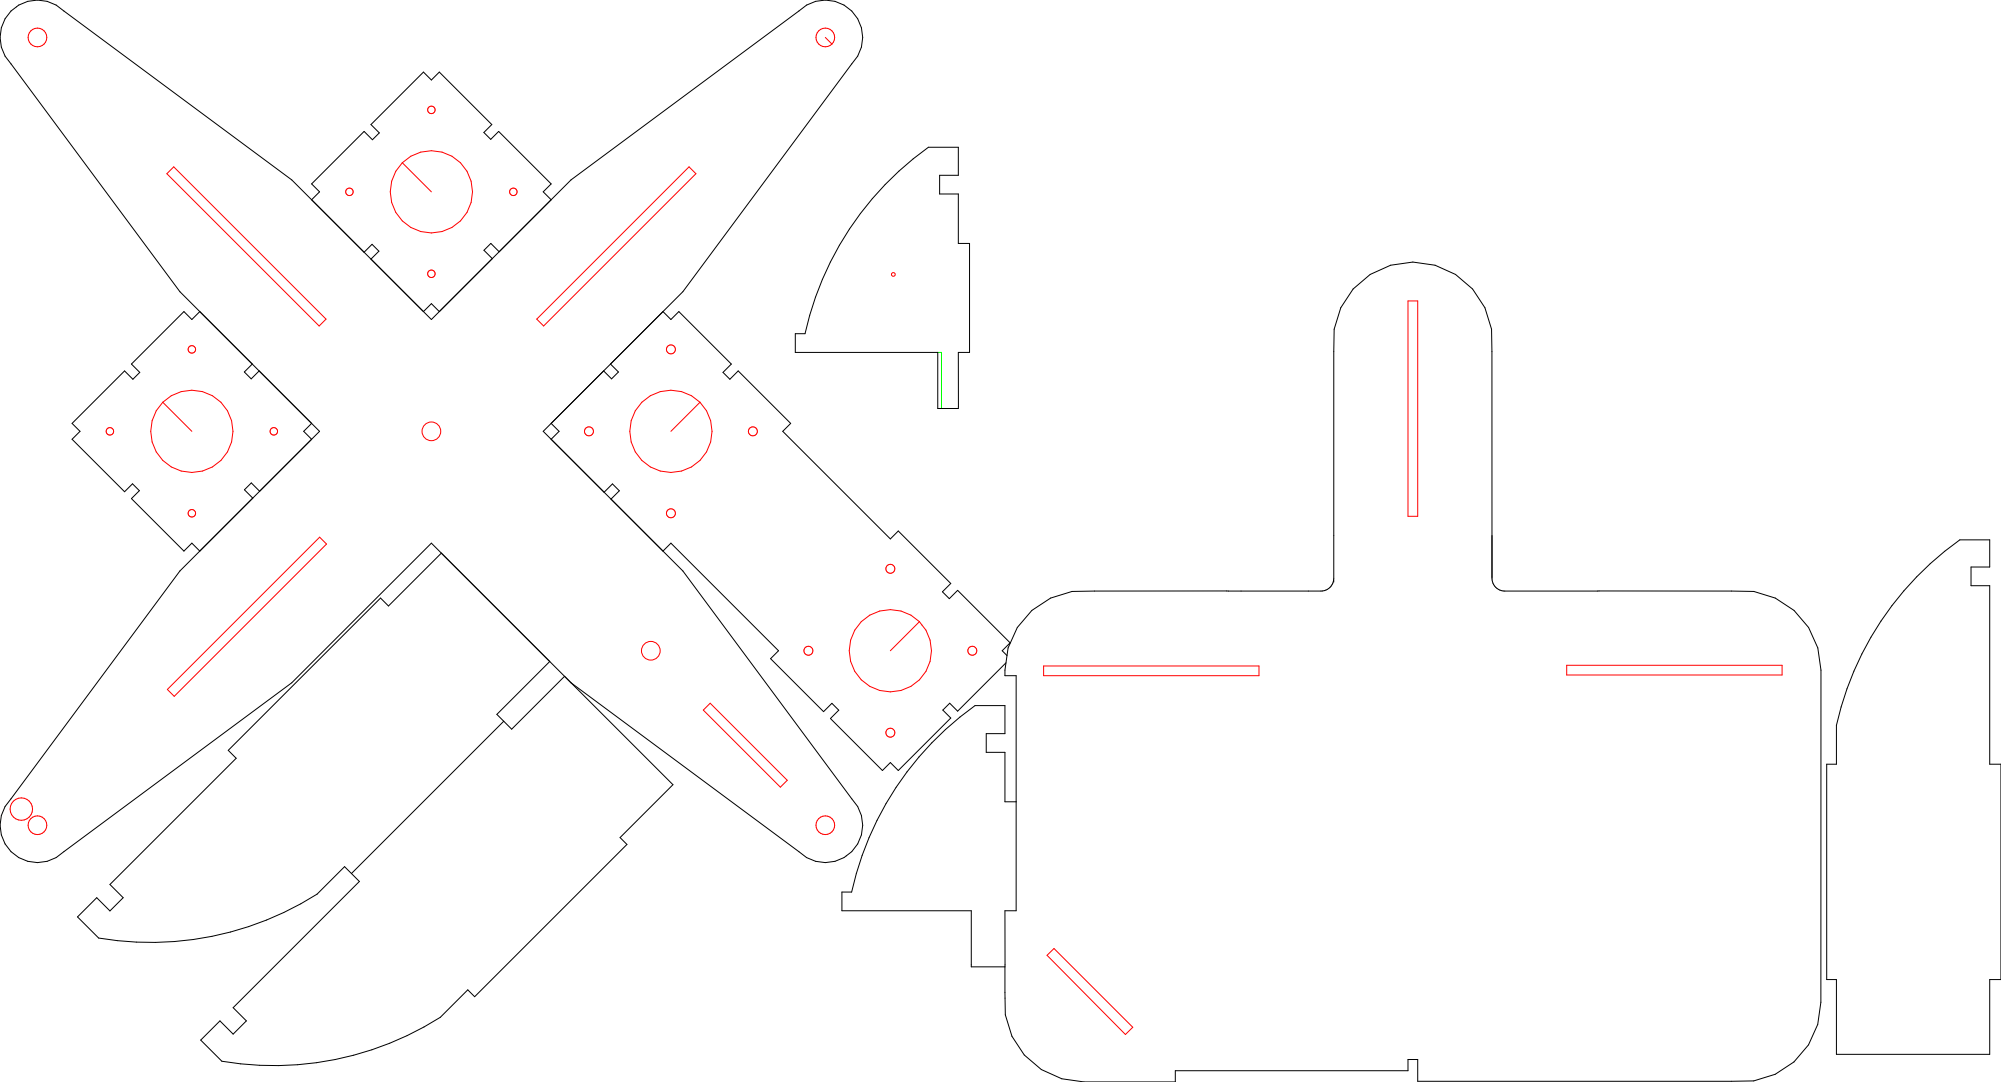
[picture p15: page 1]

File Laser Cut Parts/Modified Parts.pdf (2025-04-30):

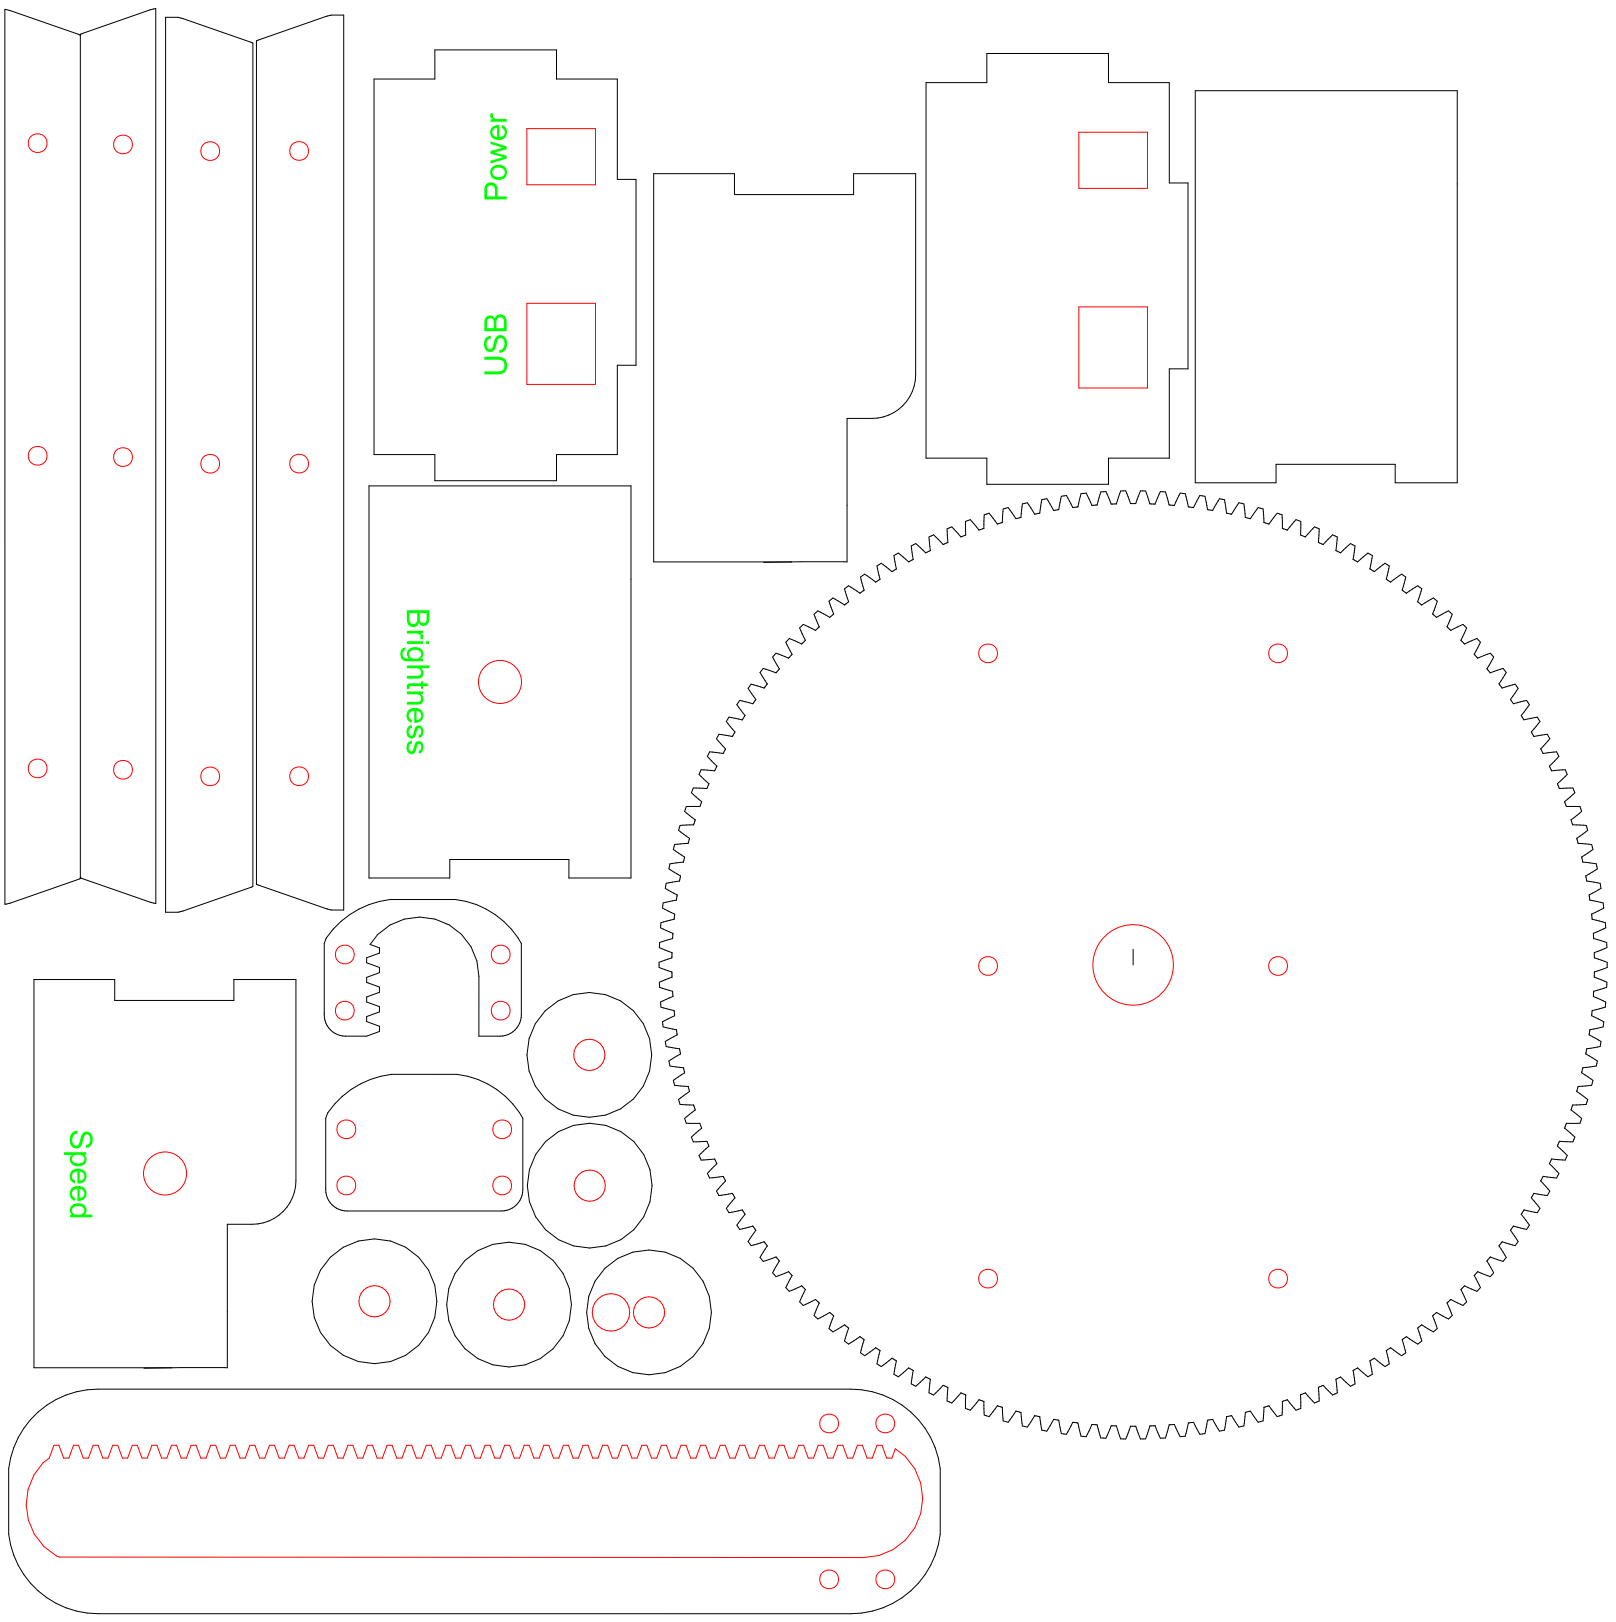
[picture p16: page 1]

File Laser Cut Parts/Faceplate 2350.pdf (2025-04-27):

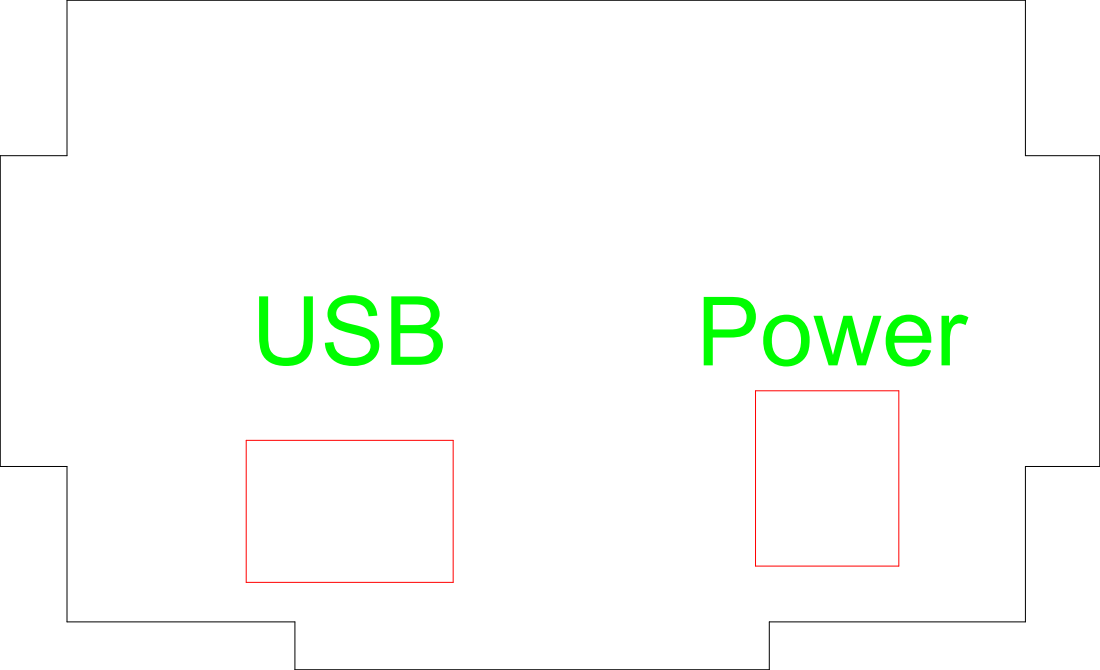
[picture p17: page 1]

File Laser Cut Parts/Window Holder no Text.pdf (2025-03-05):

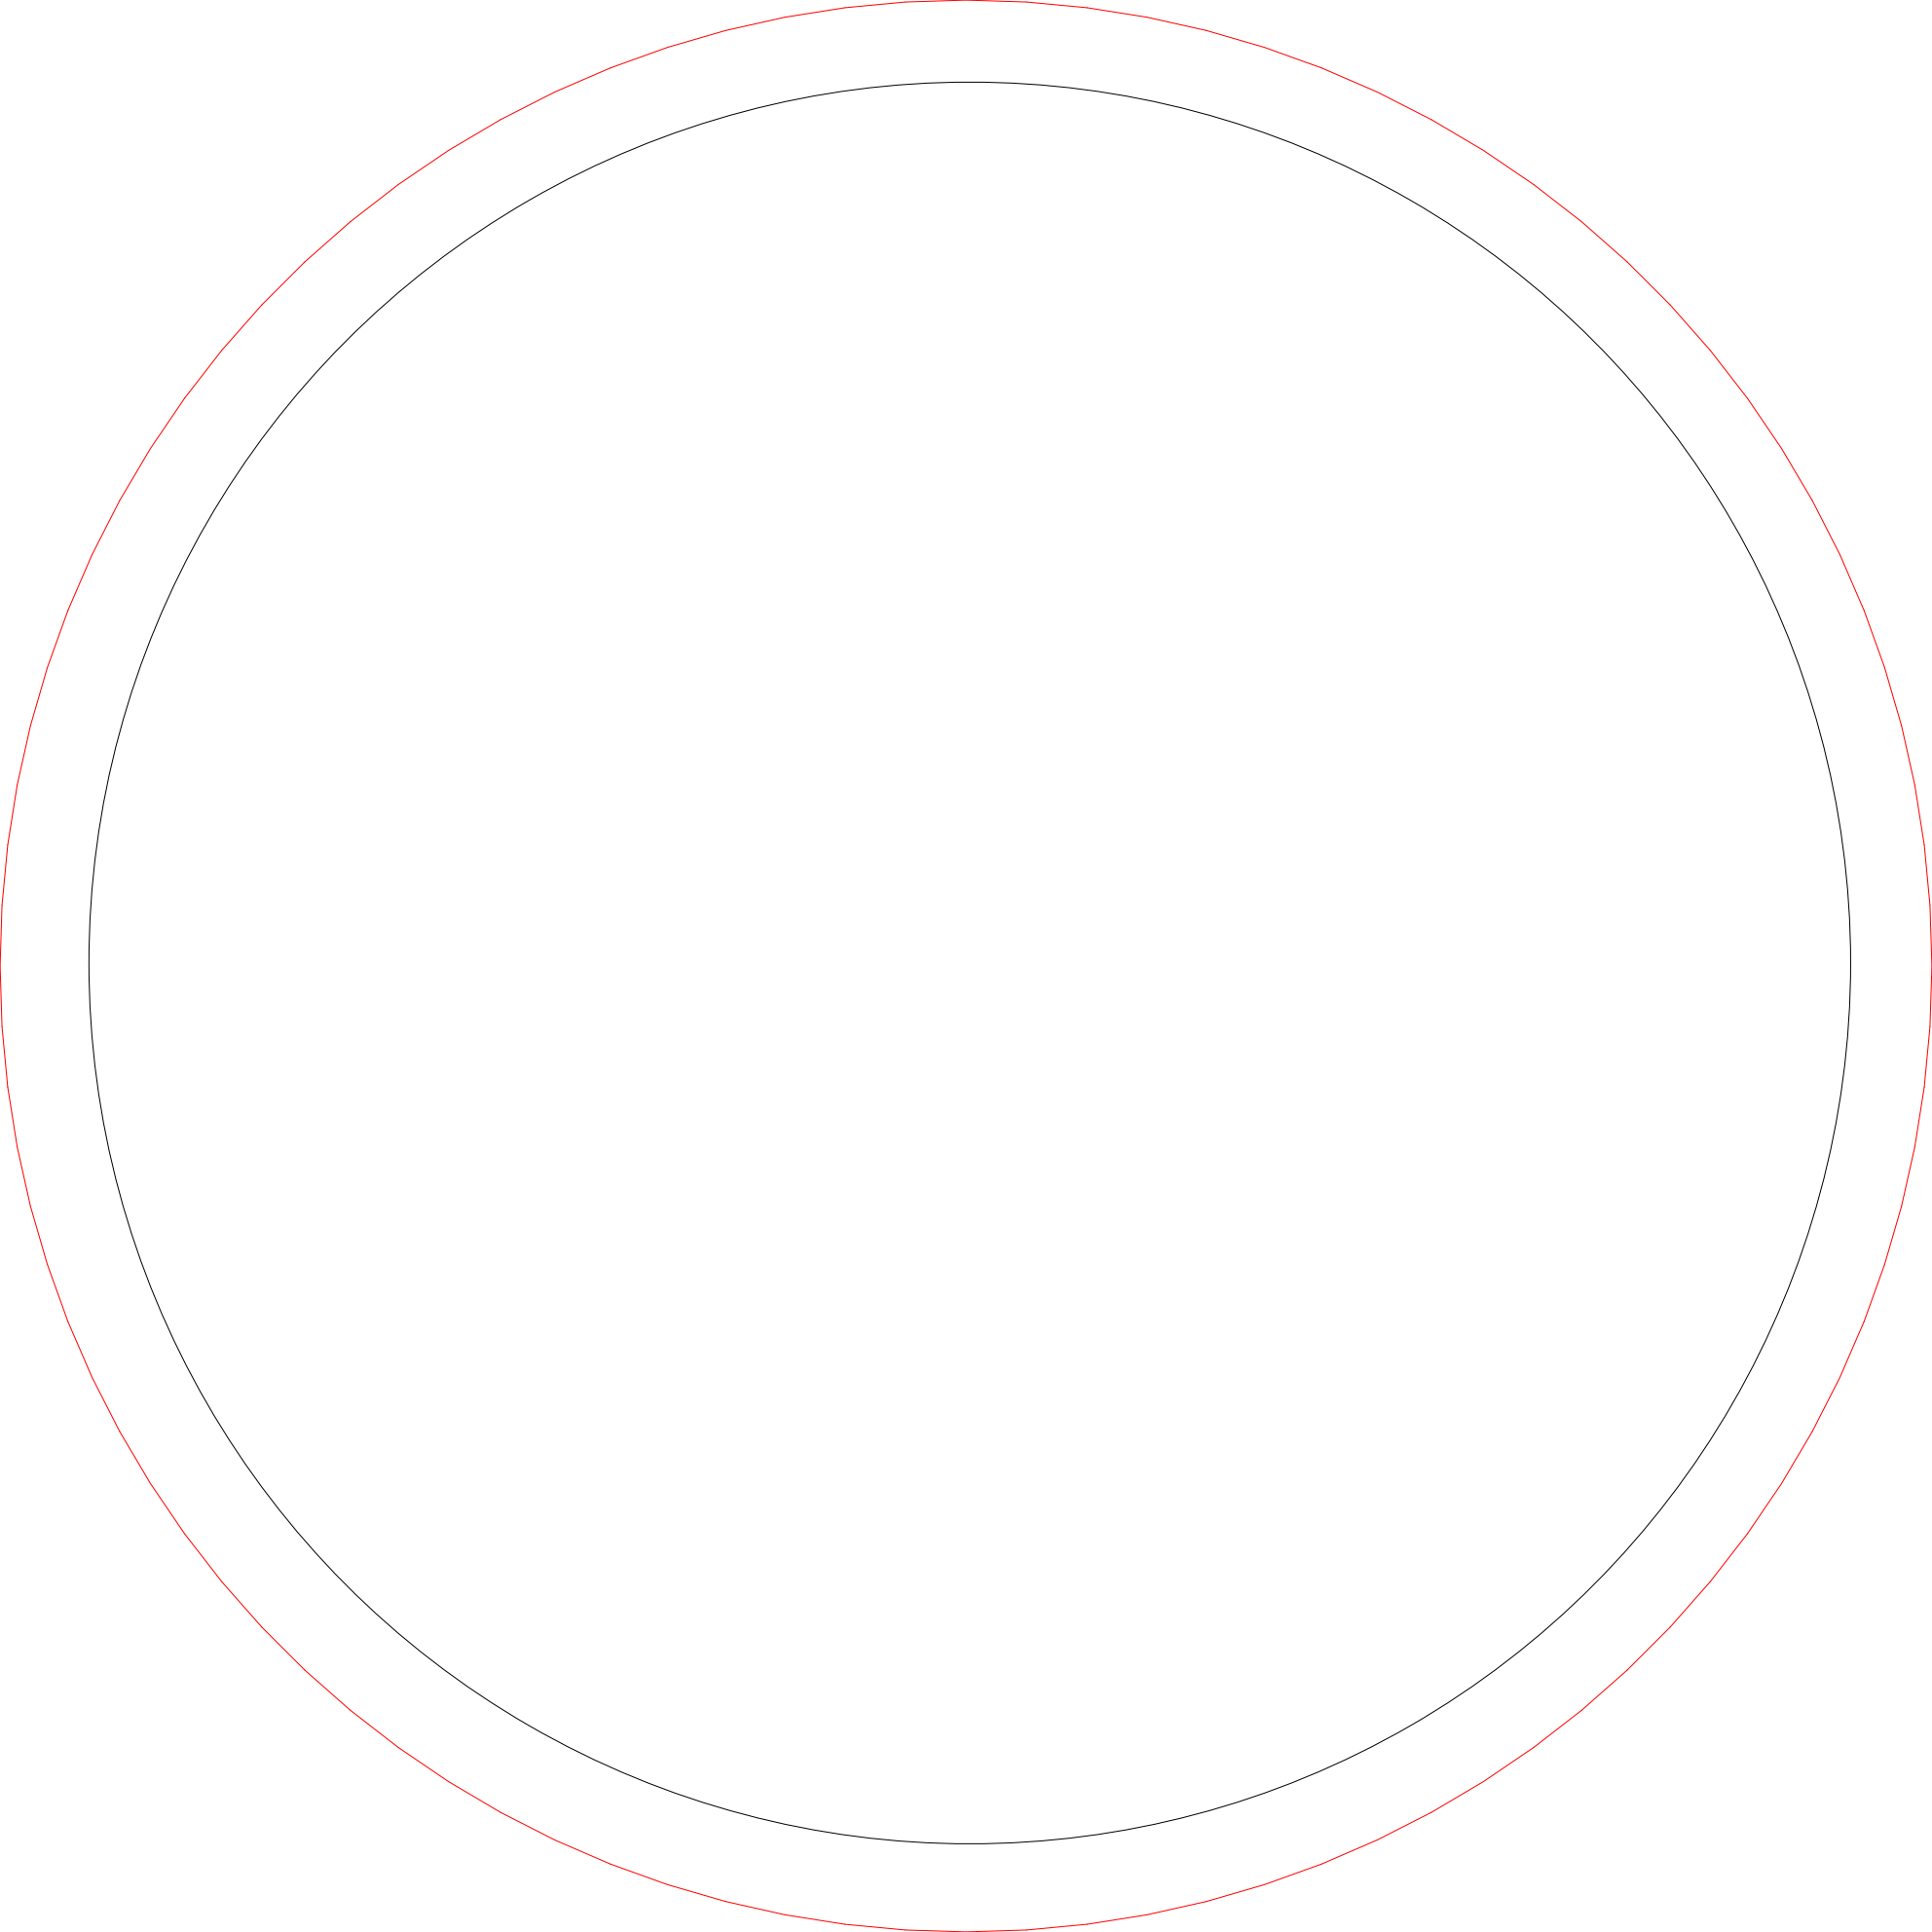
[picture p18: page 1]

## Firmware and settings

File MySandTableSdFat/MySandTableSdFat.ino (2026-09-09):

/////////////////////////////////////////////////////////////////////////////////
// MySandTableFreeRTOS.ino
//
// This file consists of an Arduino IDE sketch that is used to control the sand table
// titled "World's First Cycloid Art Table: How I Built This Arduino-Powered
// Spirograph Machine" by NewsonsElectronics.  It was published on Instructables at:
// https://www.instructables.com/Worlds-First-Cycloid-Art-Table-How-I-Built-This-Ar/
//
// The sketch supports the Adafruit Metro RP2350 processor board in conjuction
// with a CNC shield as described on Instructables.  The sketch is based on the
// original working10iteration.ino file but very heavily modified for RP2350 and
// FreeRTOS operation.  This sketch differs from the original as follows:
//   - Re-formatted, including renaming variables and functions, using consistent
//     indenting, and generally cleaning up the code.
//   - Uses Y and Z axes of the CNC shield instead of X and Y of the original.
//     This was due to the X-axis hardware on my CNC shield being damaged.
//   - Used some slightly different algorithms in a few spots.
//   - Added several more shapes, and added randomization functions for each shape.
//   - Updated for operation on RP2350 processor.
//   - Updated to use FreeRTOS.
//   - Many more changes to fix anomalous behavior and enhance operation.
//
// History:
// - 08-SEP-2026 JMC
//   - Added SD card interface.
//   - Changed Coordinate types to int_fast8_t.
//   - Fixed bug which caused catastrophic failure on ServoControlTask() timeout.
//     Was breaking out of the task's while loop and returning from the task
//     which must never be done, and caused board to lock up.
//   - Moved (most) shape files to SD card.
// - 28-AUG-2026 JMC
//   - Fixed pot scaling issue.  Was not applying low pass filter.
// - 28-AUG-2026 JMC
//   - Reworked home() operation to reduce strain on the servos.
//   - Added missing WaitForMoveComplete() calls after GotoXY().  Was causing
//     lockup after WhirlFlower() followed by MotorRatios() call.
//   - Abort shape on move timeout.
//   - Improved statistics display.
//   - Added averaging of read pot values.
// - 14-AUG-2026 JMC
//   - Replaced use of delayMicroseconds() with UsDelay().  The latest version
//     of the compiler doesn't allow delayMicroseconds() to be called within
//     critical sections.  Per earlephilhower, the SDK once did busy waits
//     (ie no IRQ needed) but it's using alarms now and doing a wfi or
//     equivalent. With interrupts disabled, that instruction will never complete.
//   - Replaced use of built-in random number generator with a library found
//     online - https://www.pcg-random.org/.  This was necessary due to the
//     built-in RNG was not thread safe, and had problems with generating
//     repeatable random sequences.
//   - Fixed incorrect display of floats due to incorrect format specifier.
//   - Reworked ShapeTask() to do all startup code within the loop.
//   - Made RandomSeed volatile since it is modified by both the shape task
//     and the remote command handling task..
//   - Fixed a few rotation display values to be degrees in place of radians.
//   - Fixed abort handling which mainly impacted ShapeTask(), ServoTask(),
//     and MotorRatios().
// - 25-JUN-2026 JMC
//   - Fixed WaitForMoveComplete() so that it waits, without timeout, for all
//     moves to be finished.
//   - After changing the random seed, check brightness to determine whether or
//     not to wipe the board.
//   - Added re-use of current random seed if none is entered when restarting.
//   - Added system up time as part of the statistics display.
//   - Minor Start/Stop Shape changes to Whirl shapes.
//   - Fixed some comments.
// - 21-JUN-2026 JMC
//   - Fixed a very subtle bug in WaitForMoveComplete() which caused motion to
//     hang when a move timed out.
//   - Added some debug logging.to Whirl().
// - 13-JUL-2026 JMC
//   - Added brightness check at power-up.  If very low brightness, then perform
//     a random wipe.  Otherwise don't bother to wipe.  This solves the problem
//     of having to wait for a lengthy wipe after every power-up, when it is
//     normally not necessary.
//   - Added FloatCoordinate structure for use with new shapes.
//   - Added Help information to HandleRemoteCommands().
//   - Added 2 new shirl shapes and supporting functions.  The whirl shape is an
//     extension of the classic "Four Mice Problem" in which four mice are
//     initially sitting at the corners of a square.  At the same time, each of
//     the mice begin running with equal speed directly toward the mouse on their
//     right.  This version extends that by starting with any number of mice at
//     any initial positions.  See:
//     https://thecalculusofexplanations.com/2022/10/09/the-four-mice-problem-2/
//     New shapes are:
//       * WhirlFlower which creates a multi sided flower composed of triangle
//         shaped whirl patterns.
//       * WhirlPoly which creates a whirl pattern based on a polygon centered
//         at the origin.
// - 21-AUG-2025 JMC
//   - Added number of points argument to all spirograph shapes.
//   - Tweaked the print queue and planner queue sizes.
//   - Increased the pausing limit check to account for analog noise.
//   - Several other minor code improvements.
// - 02-AUG-2025 JMC
//   - Replaced use of double with float_t since the floating point issue has been
//     fixed in version 2.2.0 of Piko SDK.  Result is roughly 4 x speed improvement
//     for floating point operations, but about 4kb larger memory size???
//   - Minor adjustments to shape table.
//   - Added ability to change steps per unit remotely to adjust movement smoothness.
// - 30-JUL-2025 JMC
//   - Fixed some very subtle planner and ISR issues.
//   - Increased StepsPerUnit and PLANNER_Q_LENGTH for smoother (quieter) operation.
// - 28-JUL-2025 JMC
//   - Re-worked random path selection to use RandomVoseAlias class.
//   - Fixed a couple of minor issues.
// - 12-JUL-2025 JMC
//   - Fixed limit checking in InOutServoIsr().
//   - Split servo handling into separate tasks for planning and servo controlling.
//     This allows us to queue moves ahead and eliminate delays between consecutive
//     moves due to position update calculations.
//   - Other minor repairs.
// - 28-JUN-2025 JMC
//   - Major changes to work with FreeRTOS.  Moved all serial and analog handling
//     to core 1.  Kept main path and shape generation coded on core 0.
//   - Fixed reading from the serial port in HandleRemoteCommandsTask().
//   - Made current shape invocation string fetchable via the serial port.
//   - Moved Home() call from setup to start of path task.
// - 19-MAY-2025 JMC
//   - Adjusted some delay values.
//   - Fixed RotateToAngle() to rotate in closest direction.
//   - Fixed pause LED to light when remotely paused too.
// - 18-MAY-2025 JMC
//   - Added use of PIO state machines (STStepper) to step the servos.
// - 12-MAY-2025 JMC
//   - Added pause indication via red LED.
//   - Made servo microsteps selectable via MICROSTEPS constant.
// - 27-APR-2025 JMC
//   - Original from MySandTable.ino (Arduino UNO version).  Ported to work
//     with Adafruit Metro 2350 board.  Changes include:
//       + Using fast data types since 2350 is not tight on memory.
//       + Use 1 uSec alarm timer for ISRs (UNO used 4uSec timer).
//       + Converted ISRs for 2350.
//       + Use RP2350 get_rand32() to generate starting random seed.
//       + Changed squaref() to sq() due to API differences.
//       + Changed rotary axis enable GPIO to D22 since the Metro uses D12 for
//         other functions.
//       + Changed serial logging to use single printf like macro.
//       + Reworked analog pot reading to throw away 4 LSB's due 2350's noise
//         A2D issue.
//       + Update LEDs while homing.
//       + Temporarily changed all floats and float operations to doubles to
//         work around a 2350 FPU compiler issue #2429:
//         https://github.com/raspberrypi/pico-sdk/pull/2429
//         The issue has been fixed on the development branch, but not added
//         to the release branch yet.  When it is released, this sand table
//         code will restore operation with floats, as double precision is not
//         needed.
//
// Copyright (c) 2026, Joseph M. Corbett
/////////////////////////////////////////////////////////////////////////////////
#include <limits.h>             // For UINT_MAX.
#include <FreeRTOS.h>           // For FreeRTOS core.
#include "SerialLogFreeRTOS.h"  // For data logging macro (LOG_F).
#include "STStepper.pio.h"      // For STStepper class and stepper PIO state machine.
#include "RandomVoseAlias.h"    // For RandomVoseAlias (weighted random number) class.
#include "pcg_basic.h"          // For random number generator.
#include "SdShapes.h"           // For SdShapes class.


/////////////////////////////////////////////////////////////////////////////////
// S E R I A L   L O G   S E T T I N G S
//
// The following #defines are used in conjunction with SerialLogFreeRTOS.h to
// selectively enable/disable printing of certain information.  Setting any macro
// to 'true' enables the specific level of data to be printed.  Setting any macro
// to 'false' disables printing of the specific data level.
/////////////////////////////////////////////////////////////////////////////////
#define LOG_DEBUG        false      // Log debug related info. Not normally  needed.
#define LOG_VERBOSE      false      // Log verbose info. Not normally needed.
#define LOG_INFO         true       // Log some useful extra info.
#define LOG_STEP         false      // Log data to help stepping ShapeArrays
#define LOG_CYCLES       true       // Log useful info regarding remaining cycles.
#define LOG_ALWAYS       true       // Log data unconditionally.


/////////////////////////////////////////////////////////////////////////////////
// User settable constants.
/////////////////////////////////////////////////////////////////////////////////
#define PAUSE_ON_DONE  false  // Set to 'true' to pause when drawing finishes.
#define ROT_CAUSING_IN CCW    // Set to 'CW' if clockwise rotation causes IN movement.
                              // Set to 'CCW' if counter clockwise rotation causes IN movement.
#define USE_HOME_SENSOR true  // Set to 'true' if using rotary home sensor.
#define USE_HARD_HOMING false // Set to 'true' if hard homing is desired.

// GPIO pin assignments.
const int EN_INOUT_PIN       = 8;           // Y azis (in/out) enable pin.
const int STEP_INOUT_PIN     = 3;           // Y axis (in/out) step pin.
const int DIR_INOUT_PIN      = 6;           // Y axis (in/out) direction pin.
const int EN_ROT_PIN         = 22;          // Z axis (rotation) enable pin.
const int STEP_ROT_PIN       = 4;           // Z axis (rotation) step pin.
const int DIR_ROT_PIN        = 7;           // Z axis (rotation) direction pin.
const int LIGHTS_PIN         = 11;          // Lights (LEDs) output pin.
const int PAUSE_LED_PIN      = PIN_LED;     // Pause LED lights red when paused.
const int BRIGHTNESS_POT_PIN = A0;          // Brightness pot pin.
const int SPEED_POT_PIN      = A1;          // Speed pot pin.
const int SD_CS_PIN          = 39;          // SD card chip select pin.
const int ROT_HOME_PIN       = 5;           // Home reed switch input pin.  If
                                            // USE_HOME_SENSOR is false, then this
                                            // pin is ignored and can be set to
                                            // any value.

// Hardware related constants.
const int_fast32_t  MICROSTEPS        = 64;     // Microsteps used by servos.
const int_fast32_t  ROT_TOTAL_STEPS   = 2000 * MICROSTEPS;
                                                // Rotation axis total steps.
const int_fast32_t  INOUT_TOTAL_STEPS = 537 * MICROSTEPS;
                                                // In/Out axis total steps.
const float_t       DFLT_STEPS_PER_UNIT = 10.0; // Default steps per unit.
const int_fast16_t  GEAR_RATIO        = 10;     // Ratio of rotary (big) gear to inout
                                                // (small) gear.
const float_t       MAX_SCALE_F       = 100.0;  // Maximum X or Y coordinate value.
const uint_fast32_t MAX_SCALE_I       = (uint_fast32_t)MAX_SCALE_F;
                                                // Maximum X or Y coordinate value.
const uint_fast32_t HOME_ROT_OFFSET   = 353 * (ROT_TOTAL_STEPS / 1000);
                                                // The rotational offset to be applied
                                                // after detecting the rotary home switch
                                                // while homing.
const int_fast16_t  SPEED_DELAY_MIN_VAL = 1600 / MICROSTEPS;
                                                 // Minimum axis moving delay value (uSec).
                                                 // This macro limits the maximum speed.
                                                 // Smaller numbers result in faster speed.
const int_fast16_t  SPEED_DELAY_MAX_VAL = 32000 / MICROSTEPS;
                                                 // Maximum axis speed delay value (uSec).
                                                 // Smaller numbers result in faster speed.
const uint_fast16_t MIN_FORCE_DELAY   = SPEED_DELAY_MIN_VAL;
                                                // Minimum servo update delay when forcing.
const uint_fast16_t MAX_FORCE_DELAY   = SPEED_DELAY_MAX_VAL;
                                                // Maximum servo update delay when forcing.
const float_t       WIPE_RATIO        = 9.4;    // This constant should be changed based on
                                                // ball size.  9.4 is a good value for use
                                                // with 3mm cylindrical magnet.
const uint_fast16_t WIPE_RASTER_INC   = 4;      // This constant should be changed based on
                                                // ball size.  4 is a good value for use
                                                // with 3mm cylindrical magnet.
const uint_fast32_t REMOTE_TIMEOUT_MS = 10000;  // Remote command timeout (milliseconds).
const uint_fast32_t SERVO_TIMEOUT_MS  = 60000;  // Servo completion timeout (milliseconds).

// Useful constants.
const uint_fast8_t IN              = 1;          // In/Out axis IN direction.
const uint_fast8_t OUT             = 0;          // In/Out axis OUT direction.
const uint_fast8_t CW              = 0;          // Rotation axis CLOCKWISE direction.
const uint_fast8_t CCW             = 1;          // Rotation axis COUNTERCLOCKWISE direction.
const float_t      PI_X_2          = PI * 2.0;   // Useful in many trig calculations.
const float_t      FLOAT_PRECISION = 1000.0;     // Use 3 significant digits for random floats.
const float_t      FLOAT_PRECISION_INV = 1.0/FLOAT_PRECISION;
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
void loop()
{
    vTaskDelay(pdMS_TO_TICKS(3000));
} // End loop().


/////////////////////////////////////////////////////////////////////////////////
// I N T E R R U P T   S E R V I C E   R O U T I N E S   ( I S R s)
/////////////////////////////////////////////////////////////////////////////////

/////////////////////////////////////////////////////////////////////////////////
// RotaryServoIsr()
//
// This is the ISR for the rotational motor.  This is actually an alarm callback.
// See FreeRTOS add_alarm_in_us() documentation.  It executes in the context
// of an ISR, so ISR functions are needed.
/////////////////////////////////////////////////////////////////////////////////
int64_t RotaryServoIsr(__unused alarm_id_t id, __unused void *user_data)
{
    // Only do something if rotation movement is enabled.
    if (RotOn && !Pausing)
    {
        BaseType_t taskWoken = false;

        // Step the rotary servo in the proper direction.
        RotStepper.Step(DirRot);

        // Keep track of (accumulate) the number of rotational steps based
        // direction of rotation.
        int_fast16_t offsetDir = (DirRot == ROT_CAUSING_IN) ? 1 : -1;
        InOutCompAccum += offsetDir;
        RotSteps += offsetDir;

        // Rotations cause in/out mechanical movement.  When the limit is
        // reached, we compensate by adding a step in the proper in/out
        // direction.
        if (abs(InOutCompAccum) >= GEAR_RATIO)
        {
            // Reset our compensation accumulator.
            InOutCompAccum = 0;
            if (InOutOn)
            {
                // The in/out motor is already moving.  Simply update the
                // InOutSteps counter to account for our compensation.
                InOutSteps -= offsetDir;
            }
            else
            {
                // The in/out motor is not moving.  Force our compensation
                // by actually stepping the in/out motor in the correct
                // direction.
                DirInOut = (DirRot == CW) ? IN : OUT;
                InOutStepper.Step(DirInOut);
            }
        }

        // Wrap-around conditions for rotational steps.
        if (RotSteps > ROT_TOTAL_STEPS)
        {
            RotSteps = 0;
        }
        else if (RotSteps < 0)
        {
            RotSteps = ROT_TOTAL_STEPS - 1;
        }

        // Update our (possibly new) rotational angle which is used in background
        // processing.
        RadAngle = ((float_t)RotSteps * PI_X_2) / (float_t)ROT_TOTAL_STEPS;

        // Complete the move if we've reached our target and are not using
        // multiple points.
        if (MRPointCount == 0)
        {
            if (RotSteps == RotStepsTo)
            {
                // Turn off the motor if it reaches the set point.
                RotOn = false;
            }
            if (InOutSteps == InOutStepsTo)
            {
                InOutOn = false;
            }
            if (!RotOn && !InOutOn && !MRInProcess)
            {
                xTaskNotifyFromISR(ServoCtrlHandle, 0, eNoAction, &taskWoken);
            }
        }

        portYIELD_FROM_ISR(taskWoken);
  } // End if (RotOn && !Pausing)

    // In order to restart the alarm, we return a negative delay time.  This
    // causes the timer subsystem to reschedule the alarm this many microseconds
    // from the time this ISR started.
    return -RotDelay;
} // End RotaryServoIsr().


/////////////////////////////////////////////////////////////////////////////////
// InOutServoIsr()
//
// This is the ISR for the in/out motor.  This is actually an alarm callback.
// See FreeRTOS add_alarm_in_us() documentation.  It executes in the context
// of an ISR, so ISR functions are needed.
/////////////////////////////////////////////////////////////////////////////////
int64_t InOutServoIsr(__unused alarm_id_t id, __unused void *user_data)
{
    // Only do something if in/out movement is enabled.
    if (InOutOn && !Pausing)
    {
        BaseType_t taskWoken = false;

        // Step the in/out servo in the proper direction.
        InOutStepper.Step(DirInOut);

        // Update in/out steps based on the direction.
        if (DirInOut == OUT)
        {
            InOutSteps++;
        }
        else
        {
            InOutSteps--;
        }

        // Handle the normal case of not using multiple points first.
        if (MRPointCount == 0)
        {
            // Complete the move if we've reached our target and are not
            // using multiple points.
            if (InOutSteps == InOutStepsTo)
            {
                InOutOn = false;
                if (!RotOn && !MRInProcess)
                {
                    xTaskNotifyFromISR(ServoCtrlHandle, 0, eNoAction, &taskWoken);
                }
            }
            LastMRPoints = false;
        }
        else  // MRPointCount != 0.
        {
            // First time using multiple points - remember our initial in/out
            // direction.
            if (!LastMRPoints)
            {
                LastInOutDir = DirInOut;
                LastMRPoints = true;
            }
            // Adjust the direction if limits are reached.
            if (InOutSteps >= OutLimit)
            {
                DirInOut = IN;
            }
            else if (InOutSteps <= InLimit)
            {
                DirInOut = OUT;
            }

            // If we're creating multiple points and the direction has changed,
            // deccrement the points count and notify the shape task that we're
            // done.
            if (LastInOutDir != DirInOut)
            {
                if (--MRPointCount == 0)
                {
                    RotOn   = false;
                    InOutOn = false;
                    xTaskNotifyFromISR(ShapeHandle, 0, eNoAction, &taskWoken);
                }
                // Remember the current in/out direction for next time.
                LastInOutDir = DirInOut;
            }
        } // End else (MRPointCount)

        portYIELD_FROM_ISR(taskWoken);
    } // End if (InOutOn && !Pausing)

    // In order to restart the alarm, we return a negative delay time.  This
    // causes the timer subsystem to reschedule the alarm this many microseconds
    // from the time this ISR started.
    return -InOutDelay;
} // End InOutServoIsr().

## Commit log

2025-03-05 Add files via upload
    Original creation.
    [Arduino Bumper.scad, Arduino Bumper.stl, Arduino_Bumper_0006.stl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]
2025-03-23 - Reworked shape call logging. - Renamed EndPlot() to EndShape(). - Added EndSeries() to announce the end of a series. - Added RandomLines().
    [MySandTable.ino]
2025-04-06 Increased LED PWM frequency to eliminate dimming at lower brightnesses.
2025-04-27 Updates for replacement of Arduino UNO with Adafruit Metro 2350.
    [Faceplate 2350.dxf]
2025-04-30 Added 2350 floating point test file that will be removed later, once a compiler bug is fixed. Added 3D printed Bezel. Fixed some laser cut parts. Updated Readme with latest changes.
    [Base + Large Gear.dxf, Base.dxf, Bezel3.scad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]
2025-05-05 Added 2350 Readme.md. Re-organized new 3D and Laser parts.
    [Faceplate 2350.dxf, Metro_2350_Bumper.scad, Metro_2350_Bumper.stl]
2025-05-15 Added microstep selection. Also added pause led indicator.
2025-05-18 Added use of PIO state machines to step the servos.
2025-05-19 Minor fixes: - Adjusted some delay values. - Fixed RotateToAngle() to rotate in closest direction. - Fixed pause LED to light when remotely paused too.
    [MySandTable2350.ino]
2025-06-28 - Updated to use RP2350 PIO for servo output. - Added initial code for FreeRTOS implementation. Still needs all path logic to be added.
    [Gear Hole Test 1.10.dxf, Thick Small Gear.scad, Thick Small Gear.stl]
2025-07-01 - Made current shape invocation string fetchable via the serial port. - Moved Home() call from setup to start of path task. - Minor fixes.
    [MySandTableFreeRTOS.ino]
2025-07-29 - Re-worked random path selection to use RandomVoseAlias class. - Fixed a couple of minor issues.
    [MySandTableFreeRTOSExp.ino]
2025-07-30 - Fixed some very subtle planner and ISR issues. - Increased STEPS_PER_UNIT and PLANNER_Q_LENGTH for smoother (quieter) operation.
    [MySandTableFreeRTOSExp.ino]
2025-07-30 Updated FreeRTOS version with latest fixes from exp version.
    [MySandTableFreeRTOS.ino]
2025-08-02 - Replaced use of double with float_t since the floating point issue has been fixed in version 2.2.0 of Piko SDK. Result is roughly 4 x speed improvement for floating point operations, but about 4kb 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
    [MySandTableFreeRTOSExp.ino]
2025-08-02 - Fixed all RP2350 versions to use float instead of double. Found 4 x speed improvement on float ops, but added 4kb memory use.
    [MySandTable2350.ino, MySandTableFreeRTOS.ino]
2025-08-10 - Completed readme file for Exp version. - Some minor updates and fixes.
    [MySandTableFreeRTOSExp.ino]
2025-08-21 - Added number of points arguments to all spirograph shapes. - Tweaked the print queue and planner queue sizeds. - Increased the pausing limit check to account for analog noise. - Several other minor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
    [MySandTableFreeRTOSExp.ino]
2026-06-21 Fixed WaitForMoveComplete() hang bug.
    [MySandTableFreeRTOSExp.ino]
2026-06-26 Fixed WaitForMoveComplete() bug, plus other minor fixes.
    [MySandTableFreeRTOSExp.ino]
